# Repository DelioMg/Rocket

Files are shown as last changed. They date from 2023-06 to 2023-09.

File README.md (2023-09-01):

# Mini Foguete

Projeto de desenvolvimento de um Minifoguete com Base em Sistemas de Massa Variável para Materia de Fisica Experimental A.
 
O projeto consiste em uma abordagem sistemática para o desenvolvimento e aprimoramento de foguetes em miniatura, utilizando uma metodologia que envolve aquisição de dados, cálculo de velocidade do foguete e comparação com dados reais obtidos durante os testes com intenção de demonstrar o funcionamento do momento linear em um sistema de massas variáveis. O projeto consiste na obtenção de propelente para realizar teste e através dos dados obtidos calcular velocidade que o foguete pode atingir que após esses será realizado o lançamento de mini foguete e obtenção dos dados de voo para comparação com resultado obtido com cálculo.  

Etapas :
1. Aquisição do Motor. 
2. Teste Estático do Motor
3. Desenvolvimento de uma Avionica para aferição da Altitude.
4. Desenvolvimento do Minifoguete: Utilizando um modelo 3D como base com ajuste para acomodar uma aviônica.
5. Com Massa do Minifoguete Calcular a Velocidade.
6. Lançar o Foguete.
7. Comparar os Dados.

## 1. Motor.

Por já ter conhecimento na produção do motor não foi preciso comprar, em que foi produzido KNSu e a carcaça do motor feita com cano de PVC de 3/4.

## 2. Teste Estatico 

Para realização do Teste estatico foi utilizada uma celula de carga de 10Kg com Hz711 modificado para 80hz para melhor precisão das leituras obtendo os resultados Abaixo:

## 3.Avionica 

Nesta etapa do projeto, foi desenvolvida uma PCB utilizando o software Eagle. A PCB tem como objetivo realizar a aferição da altitude durante o voo e envio dos dados para uma base remota. A placa utiliza componentes específicos para cada função, como o microcontrolador ESP8266 para cálculos, o sensor BMP280 para medição de altitude e temperatura, o sensor MPU6050 para medição de aceleração, o módulo NRF24L01+ para transmissão dos dados, um slot de Micro SD para funcionar como datalogger do voo, reguladores de tensão para ajustar a voltagem de 3,7V para 3,3V, um circuito para aferição da tensão da bateria, um circuito para acionar o paraquedas e um buzzer. Além disso, são utilizadas duas baterias de 3,7V para alimentação da placa.

## 4.Desenvolviemto do Minifoguete 

Nesta etapa do projeto, foi utilizado o modelo de foguete 3D Modular Model Rocket disponível no Thingiverse, que pode ser encontrado no seguinte link: [3D Modular Model Rocket](https://www.thingiverse.com/thing:8754).

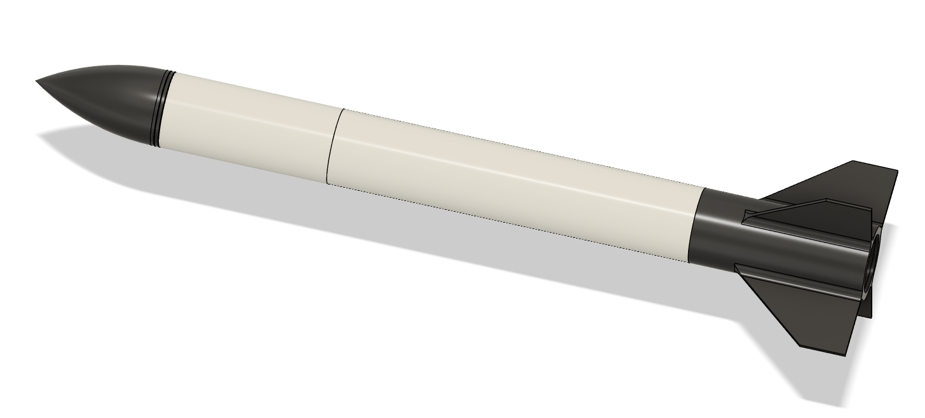
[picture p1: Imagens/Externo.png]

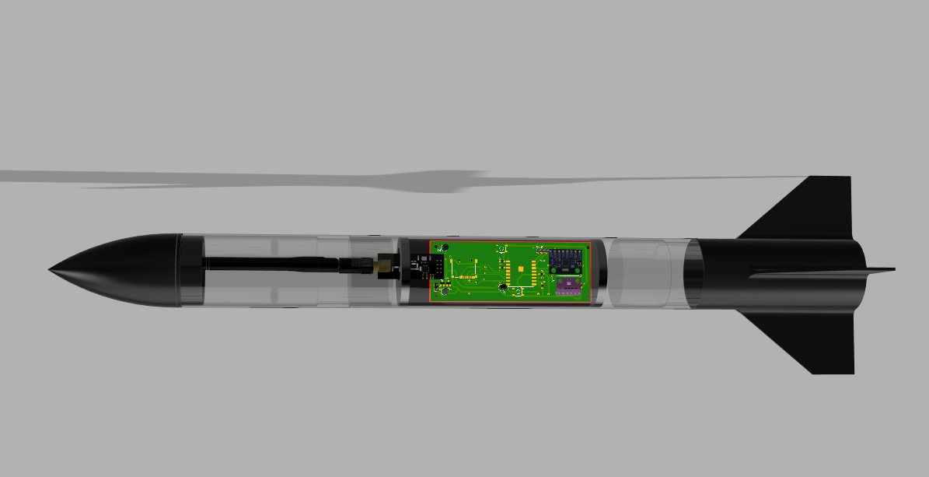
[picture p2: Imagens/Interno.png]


Esse modelo de foguete foi modificado para permitir o acoplamento de diferentes tamanhos de motores. Além disso, o programa OpenRocket foi utilizado para ajustar a estabilidade do MiniFoguete.

## 5.Calculos

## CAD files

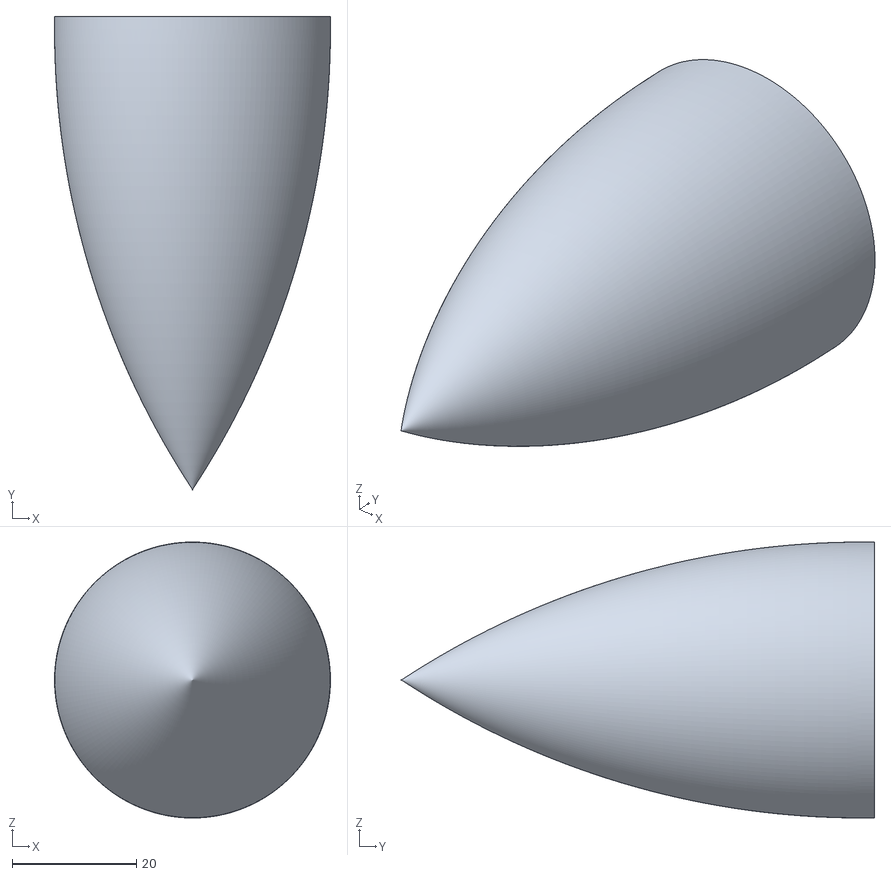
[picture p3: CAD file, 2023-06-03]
3Dimprimivel/Coifa.stl
44.4 x 76.2 x 44.4

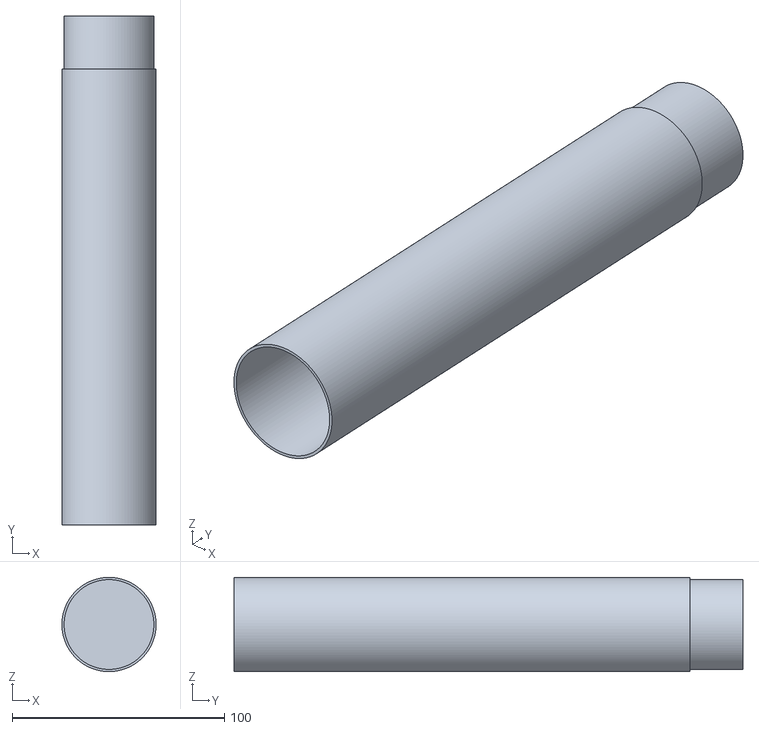
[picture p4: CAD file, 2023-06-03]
3Dimprimivel/Tubomaior.stl
44.4 x 240.0 x 44.5

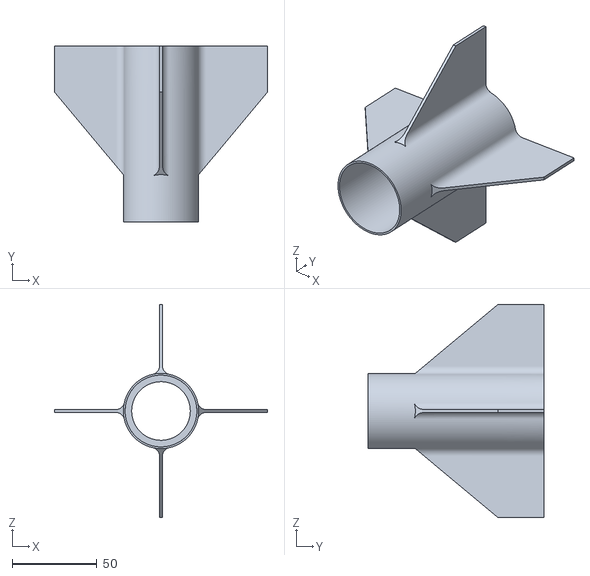
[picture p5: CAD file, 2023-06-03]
3Dimprimivel/Aletas.stl
125.7 x 103.6 x 125.7

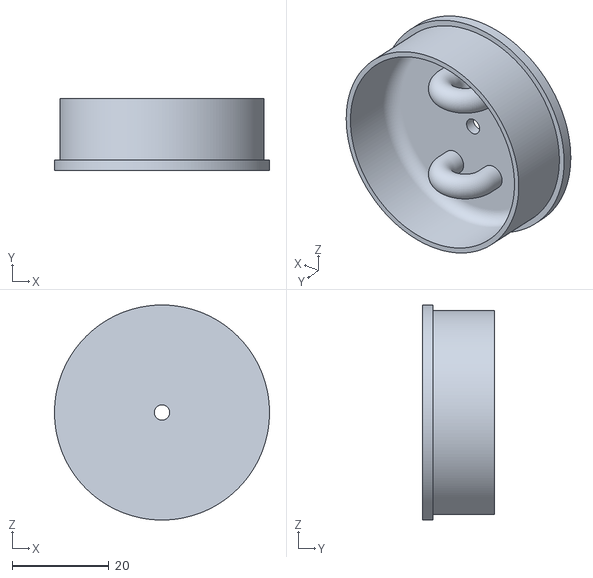
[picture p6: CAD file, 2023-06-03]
3Dimprimivel/Acoplador.stl
44.4 x 14.8 x 44.4

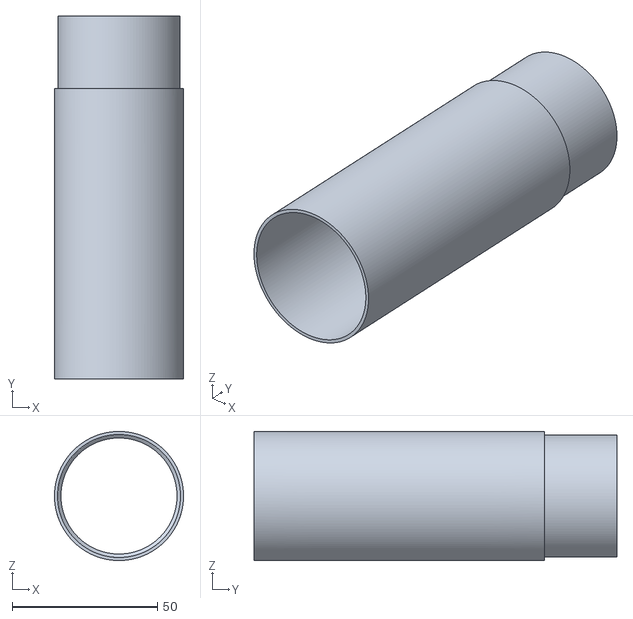
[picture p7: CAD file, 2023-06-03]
3Dimprimivel/Tubomenor.stl
44.4 x 125.0 x 44.5

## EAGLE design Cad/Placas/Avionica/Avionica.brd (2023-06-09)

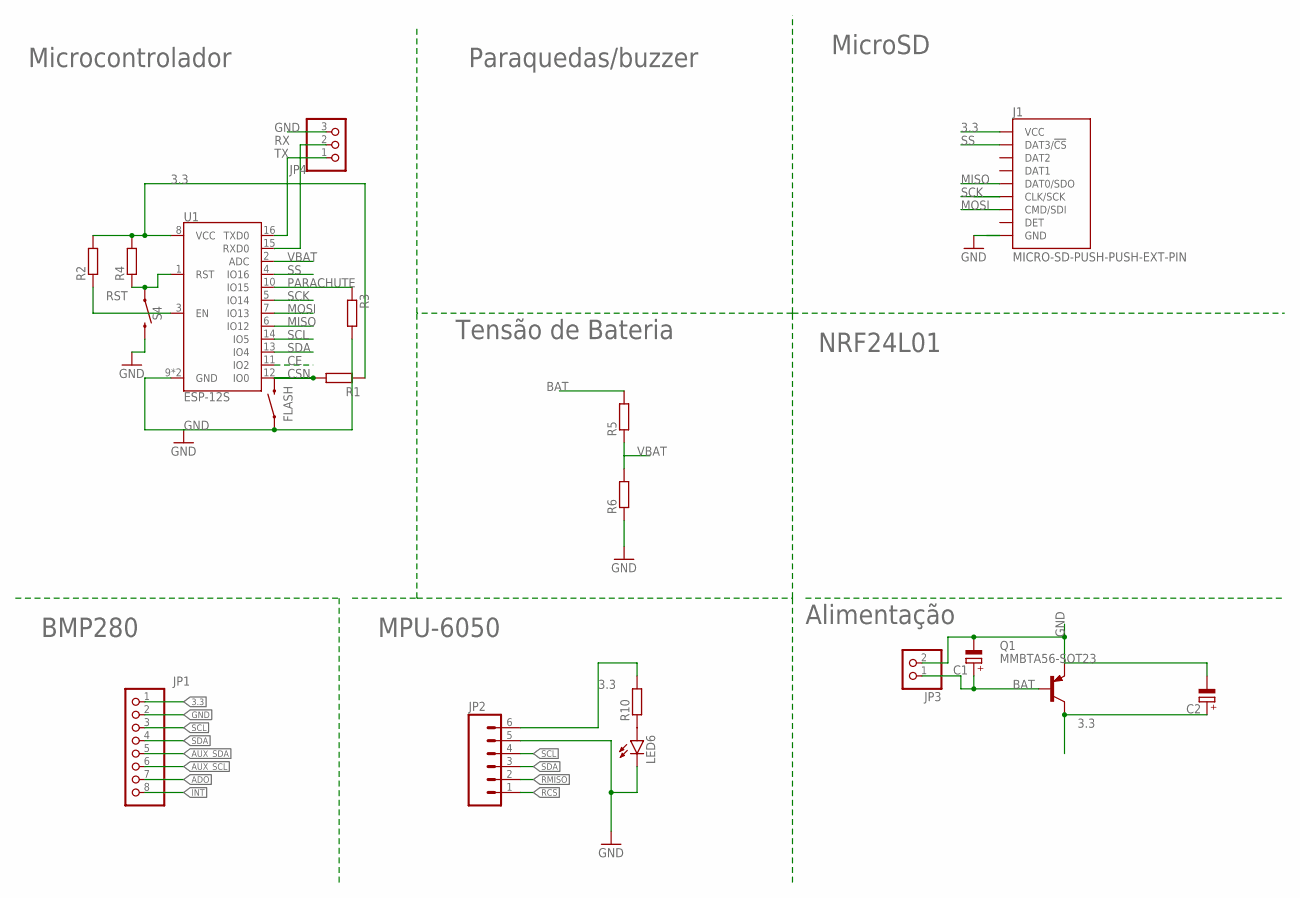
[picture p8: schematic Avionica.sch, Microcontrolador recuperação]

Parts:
C1, C2: CPOL-EUE1.8-4; E1,8-4
FLASH: MOMENTARY-SWITCH-SPST-SMD-5.2MM-TALL; TACTILE_SWITCH_SMD_5.2MM
J1: MICRO-SD-PUSH-PUSH-EXT-PIN; MICROSD-EXTERNALPIN
JP1: PINHD-1X8; 1X08
JP2: M06NO_SILK_FEMALE_PTH; 1X06_NO_SILK
JP3: PINHD-1X2; 1X02
JP4: PINHD-1X3; 1X03
LED6: LEDCHIP-LED0805; CHIP-LED0805
Q1: MMBTA56-SOT23; SOT23
R1, R2, R3, R4: R-EU_R0805W; R0805W
R5, R6, R10: R-EU_M0805; M0805
S4: MOMENTARY-SWITCH-SPST-SMD-5.2MM-TALL; TACTILE_SWITCH_SMD_5.2MM
U1: ESP-12S

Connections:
3.3: C2.+, J1.4 (VCC), JP1.1, JP2.6, Q1.3 (C), R1.2, R2.2, R4.2, R10.2, U1.8 (VCC)
ADO: JP1.7
AUX_SCL: JP1.6
AUX_SDA: JP1.5
BAT: C1.+, JP3.1, Q1.1 (B), R5.2
CE: U1.11 (IO2)
CSN: FLASH.3 (2), R1.1, U1.12 (IO0)
EN: R2.1, U1.3 (EN)
GND: C1.-, C2.-, FLASH.1, J1.6 (GND), J1.10 (GND), J1.11 (GND), J1.12 (GND), J1.13 (GND), JP1.2, JP2.5, JP3.2, JP4.3, LED6.C, Q1.2 (E), R3.2, R6.1, S4.3 (2), U1.9 (GND), U1.P$1 (GND)
INT: JP1.8
MISO: J1.7 (DAT0/SDO), U1.6 (IO12)
MOSI: J1.3 (CMD/SDI), U1.7 (IO13)
unnamed: LED6.A, R10.1
PARACHUTE: R3.1, U1.10 (IO15)
RCS: JP2.1
RMISO: JP2.2
RST: R4.1, S4.1, U1.1 (RST)
RX: JP4.2, U1.15 (RXD0)
SCK: J1.5 (CLK/SCK), U1.5 (IO14)
SCL: JP1.3, JP2.4, U1.14 (IO5)
SDA: JP1.4, JP2.3, U1.13 (IO4)
SS: J1.2 (DAT3/!CS!), U1.4 (IO16)
TX: JP4.1, U1.16 (TXD0)
VBAT: R5.1, R6.2, U1.2 (ADC)

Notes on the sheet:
BMP280
MPU-6050
Alimentação
MicroSD
Paraquedas/buzzer
Microcontrolador
Tensão de Bateria
NRF24L01

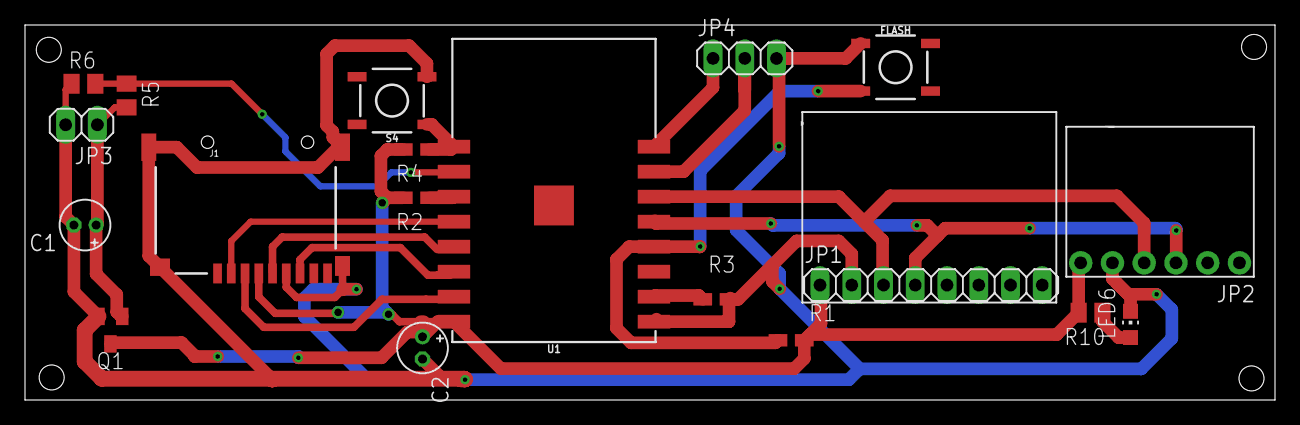
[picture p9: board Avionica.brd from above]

Board: 2 copper layers, 100.0 x 30.0 mm, 19 parts (0 on the bottom side), 17 nets.

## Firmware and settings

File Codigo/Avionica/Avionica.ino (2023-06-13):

/*
Transmissão simples constatante de pacote de 32 bytes 

Conexões com Esp8266

nRF24L01  
 1 - GND
 2 - VCC-3.3V
 3 - CE-D4 
 4 - CSN-D8
 5 - SCK-D5
 6 - MOSI-D7
 7 - MISO-D6

BMP280
 1 - VCC - 3.3V
 2 - GND
 3 - SCL
 4 - SDA

MPU6050
 1 - VCC-3.3V
 2 - GND
 3 - SCL-D1
 4 - SDA-D2

SD
 1 - GND
 2 - VCC-3.3V
 3 - MISO-D6
 4 - MOSI-D7
 5 - SCK-D5
 6 - CS-D0

Paraquedas/Buzzer
1-D3(GPIO0)
*/

#include <SPI.h>
#include <nRF24L01.h>
#include <RF24.h>
#include <Wire.h>
#include <Adafruit_BMP280.h>
#include <Adafruit_MPU6050.h>
#include <Adafruit_Sensor.h>
#include <SD.h>   

//Configuração dos Modulos 

Adafruit_MPU6050 mpu;
const uint64_t pipeOut =  0xE8E8F0F0E1LL;
Adafruit_BMP280 bmp; // I2C

// O tamanho deste pacote não deve exceder 32 bytes
struct PacketData {
  unsigned long mill;
  float altmp;
  float temp;
  float pres;
  float alt;
  float vaalt;
  float acz;
  int parachute; 
// 4+4+4+4+4+4+4+4=32bytes  
  };

File myFile;
PacketData data;

RF24 radio(12, 2); //CE-CSN

//====================================================================================

//------------------------------------------------------------------------------------
// inicialização do SD
//------------------------------------------------------------------------------------

void sdini() {
  Serial.print("Inicializando o cartão SD...");
  // verifica se o cartão SD está presente e se pode ser inicializado

  
  if (!SD.begin(5)) { // ESP8266 GPIO16 D0
    // programa encerrado 
    Serial.println("Falha, verifique se o cartão está presente.");
    return;                                                      
  }

  // Cria arquivo data.txt e abre
  myFile = SD.open("/data.txt", FILE_APPEND);                        
  // Escreve dados no arquivo
  if (myFile) {
    Serial.print("Gravando...");
    myFile.println("Tempo, Temperatura , Altitude, VAltitude , AceZ, Altitudemp, Pressão, Paraquedas");
    myFile.close();

  } else {
    Serial.println("Error ao abrir data.txt");

  }
}
//====================================================================================

//------------------------------------------------------------------------------------
// Grava dados em formato de string
//------------------------------------------------------------------------------------

void writeOnSD(String str) {
  myFile = SD.open("/data.txt", FILE_APPEND);

  if (myFile) {
    Serial.println("(OK)");
    myFile.println(str);
    myFile.close();

  } else {
    Serial.println("Error ao gravar em data.txt");

  }
}
//====================================================================================
float altini;
void setup() {
  
  //Configuração do NRF24L01+
  radio.begin();
  radio.setAutoAck(false);
  radio.setDataRate(RF24_250KBPS);
  radio.openWritingPipe(pipeOut);
  //Chama a função que incializa o Sd
  sdini();
  //zera os dados da struct
  data.mill = 0;
  data.altmp = 0;
  data.temp= 0;
  data.pres= 0;
  data.alt= 0;
  data.vaalt= 0;
  data.acz= 0; 
  altini=0;  
  //Inicializa a serial
  Serial.begin(115200);
  //Configura o BMP280
  while ( !Serial ) delay(100);   // wait for native usb
  Serial.println(F("BMP280 test"));
  unsigned status;
  status = bmp.begin(BMP280_ADDRESS_ALT, BMP280_CHIPID);
  status = bmp.begin();
  if (!status) {
    Serial.println(F("Could not find a valid BMP280 sensor, check wiring or "
                      "try a different address!"));
    Serial.print("SensorID was: 0x"); Serial.println(bmp.sensorID(),16);
    Serial.print("        ID of 0xFF probably means a bad address, a BMP 180 or BMP 085\n");
    Serial.print("   ID of 0x56-0x58 represents a BMP 280,\n");
    Serial.print("        ID of 0x60 represents a BME 280.\n");
    Serial.print("        ID of 0x61 represents a BME 680.\n");
    while (1) delay(10);
  }
  //Configura o MPU6050
  /* Default settings from datasheet. */
  bmp.setSampling(Adafruit_BMP280::MODE_NORMAL,     /* Operating Mode. */
                  Adafruit_BMP280::SAMPLING_X4,     /* Temp. oversampling */
                  Adafruit_BMP280::SAMPLING_X8,    /* Pressure oversampling */
                  Adafruit_BMP280::FILTER_X16,      /* Filtering. */
                  Adafruit_BMP280::STANDBY_MS_63); /* Standby time. */

  mpu.setAccelerometerRange(MPU6050_RANGE_8_G);
  switch (mpu.getAccelerometerRange()) {
  case MPU6050_RANGE_2_G:
    break;
  case MPU6050_RANGE_4_G:
    break;
  case MPU6050_RANGE_8_G:
    break;
  case MPU6050_RANGE_16_G:
    break;
  }
  mpu.setGyroRange(MPU6050_RANGE_500_DEG);
  switch (mpu.getGyroRange()) {
  case MPU6050_RANGE_250_DEG:
    break;
  case MPU6050_RANGE_500_DEG:
    break;
  case MPU6050_RANGE_1000_DEG:
    break;
  case MPU6050_RANGE_2000_DEG:
    break;
  }

  mpu.setFilterBandwidth(MPU6050_BAND_21_HZ);
  switch (mpu.getFilterBandwidth()) {
  case MPU6050_BAND_260_HZ:
  break;
  case MPU6050_BAND_184_HZ:
   break;
  case MPU6050_BAND_94_HZ:
   break;
  case MPU6050_BAND_44_HZ:
   break;
  case MPU6050_BAND_21_HZ:
   break;
  case MPU6050_BAND_10_HZ:
   break;
  case MPU6050_BAND_5_HZ:
   break;
  }

  altini=bmp.readAltitude(1017.3);

  delay(100);  
    
}


void loop() {

  //Armazena o tempo do microcontrolador.
  data.mill= millis()/1000;
  //Medições BMP280
  data.temp= bmp.readTemperature();
  data.pres= bmp.readPressure();
  data.alt= bmp.readAltitude(1017.3);
  data.vaalt= bmp.readAltitude(1017.3)-altini;
  //Medições MPU6050
  sensors_event_t a, g, temp;
  mpu.getEvent(&a, &g, &temp);
  data.acz= a.acceleration.z;  

  //Grava e transmiti os dados:
  String dados = String(data.mill,3)+","+String(data.temp, 3)+","+String(data.alt, 3)+","+String(data.vaalt, 3)+","+String(data.acz, 3)+","+String(data.altmp, 3)+","+String(data.pres, 3)+","+String(data.parachute);
  writeOnSD(dados); //Grava no cartão sd
  Serial.println(dados); //printa os Dados
  radio.write(&data, sizeof(PacketData)); //transmite o pacote  
  delay(50);  
}

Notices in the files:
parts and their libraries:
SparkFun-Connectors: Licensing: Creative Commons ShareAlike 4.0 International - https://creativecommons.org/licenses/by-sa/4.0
